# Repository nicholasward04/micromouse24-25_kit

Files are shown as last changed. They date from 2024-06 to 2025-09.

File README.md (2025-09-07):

The following repository will contain the work I've done as lead of the UCI Micromouse program. Some of the files included are inaccessible shortcuts and are generally administrative in nature. If you would like access please contact me at 818-233-1594 or nnward2004@icloud.com. 

The PCB is iterative and has had 2 other collaborators work on it in previous years. The PCB design was done in KiCAD 7.0 and the STM32 will be programmed using the STM32CubeIDE. I've changed the motor driver to something more capable than the L293D, added a circuit to protect the microcontroller when both the battery and STLINK are being used in full, and added an extra button. The PCB is 4-layer board with 3 GND planes and 1 power plane (split into +5V and +3V3 sections). I rerouted the entire board to fit in the new circuitry while maintaining the legacy aspects of the schematic. 
There are 2 versions of the design, one using an STM32 bluepill and one using solely the STM32F103C8T6 chip. This is to provide the option for teams that are part of the program to route their own boards using either one. 

Below is the relevant schematic.


Version using STM32 Bluepill front and back. The middle 2 layers of the board are mostly empty asides from a few traces and a GND and power plane, and therefore will not be included by image.

  

Version using STM32F103C8T6 chip front and back. Same as previous in terms of middle 2 layers. 

  

The software is split into 3 main components:
  1. The simulation
  2. The debugging GUI
  3. The firmware
<br>
1. The first part I worked on was my maze-solving algorithm in mackorone's micromouse simulator (https://github.com/mackorone/mms). Below is a gif of such:
Example
<br>
2. In parallel with the firmware, I developed a debugging tool using the Python Tkinter library, communicating with a UART bluetooth module on board my micromouse. This tool wasn't fully completed, but was useful for viewing telemetry from my mouse, such as IR sensor readings and battery voltage. If I were to do it again, I would have developed it in Visual Studio using C#, since the toolkits are much more advanced and easier to work with. Nevertheless, it was a good experience implementing wireless communication across a UART serial interface. Below is an image of the tool:
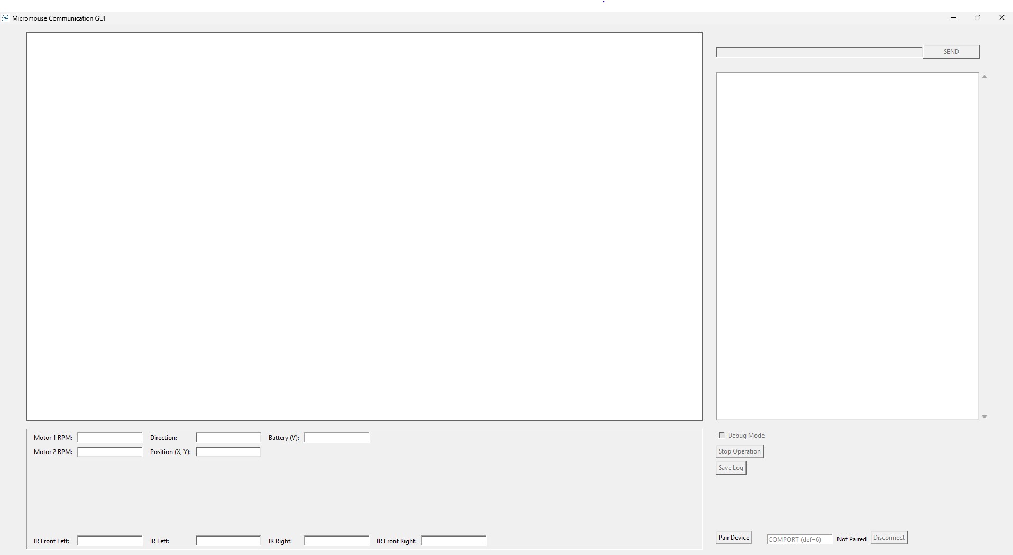
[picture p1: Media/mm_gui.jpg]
Example

<br>
3. Lastly, and most importantly, the firmware for my mouse was devleoped in C using the STM32CubeIDE. Below is a link to my best run at competition, where I placed 4th overall:
  
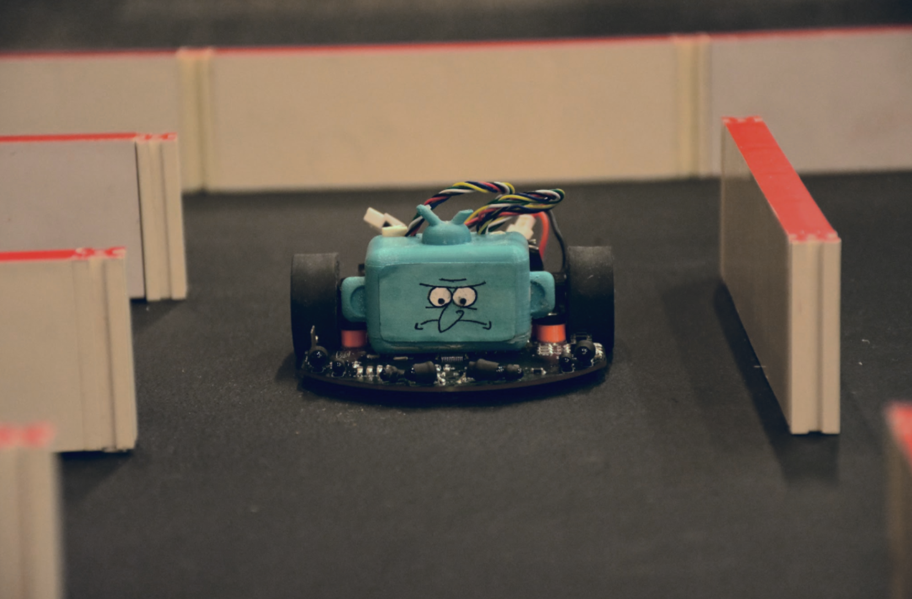
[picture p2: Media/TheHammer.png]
(https://www.youtube.com/live/5uL4w6jP68s?si=986Pjw4Ats6Im9Sl&t=11015)


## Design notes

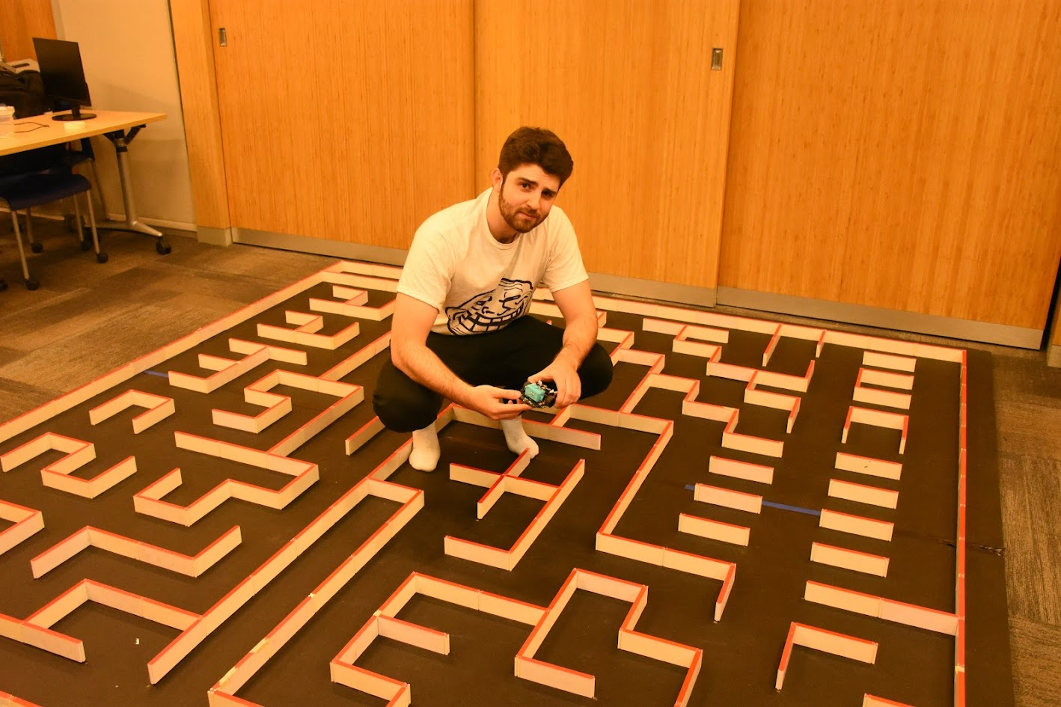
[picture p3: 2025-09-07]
Media/AAMC_2025.png

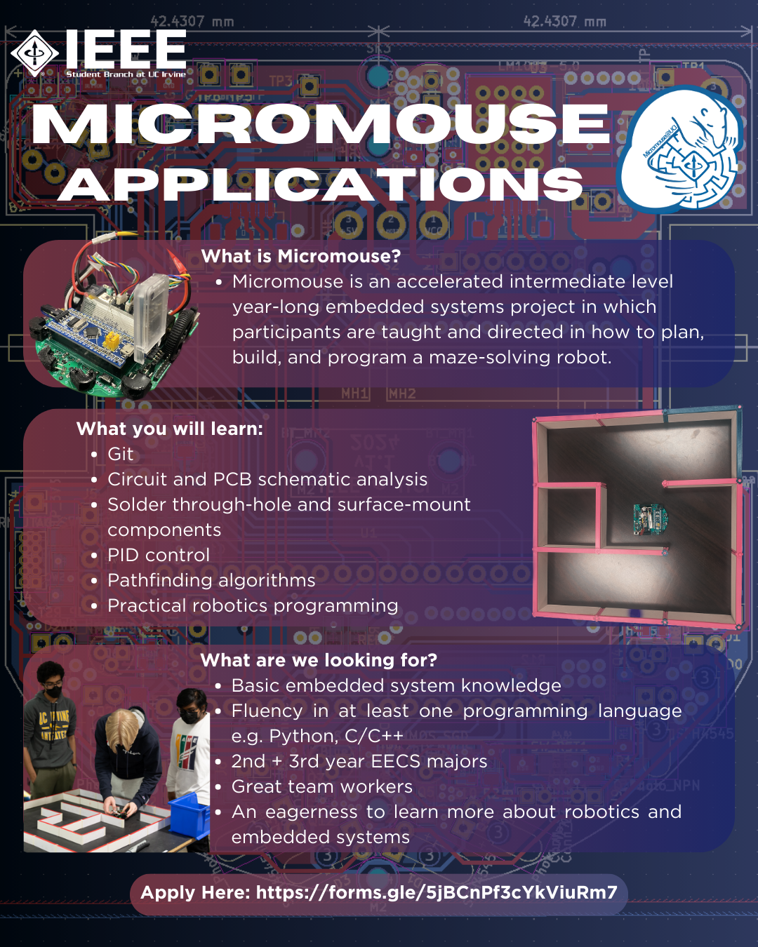
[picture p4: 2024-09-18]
Promotional/mm_flier_24-25no_qr.png

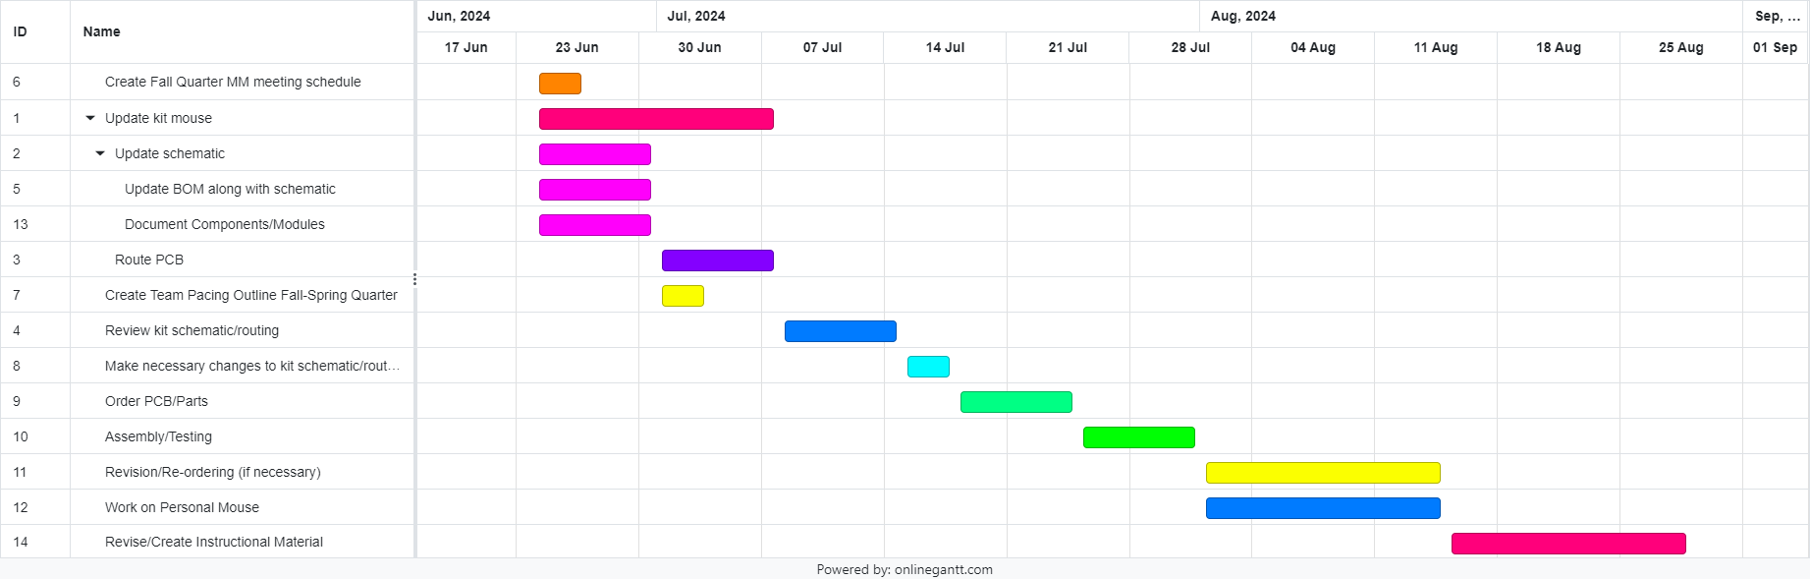
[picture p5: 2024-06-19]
Scheduling/MM24-25GanttChart_NW.png

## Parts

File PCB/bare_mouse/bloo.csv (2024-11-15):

Id | Designator | Footprint | Quantity | Designation | Supplier and ref
1 | D5,D4,D6 | LED_0805_2012Metric_Pad1.15x1.40mm_HandSolder | 3 | LED
2 | BZ1 | MagneticBuzzer_PUI_AT-0927-TT-6-R | 1 | Buzzer
3 | Q1,Q0,Q3,Q2 | Emitter | 4 | Q_Photo_NPN
4 | SW_RST1,SW2,SW1,SW3 | SW_SPST_REED_CT05-XXXX-G1 | 4 | SW
5 | D1,D3,D2,D0 | Emitter | 4 | SFH4545
6 | TP5,TP6,TP2 | PinHeader_1x01_P2.54mm_Vertical | 3 | GND_TP
7 | Q10,Q11,Q12,Q9 | SOT-23 | 4 | Q_NMOS_GSD
8 | BT1 | PinSocket_1x02_P2.54mm_Vertical | 1 | Battery_Cell
9 | J1 | PinHeader_1x06_P2.54mm_Vertical | 1 | Serial Debug Header
10 | R6,R8,R5,R7 | R_1206_3216Metric_Pad1.30x1.75mm_HandSolder | 4 | 35
11 | MOS1 | SOT-23F_TOS | 1 | SSM3K335R_LF
12 | J5,J2 | PinHeader_1x05_P2.54mm_Vertical | 2 | SWD Header
13 | C3,C21,C18,C15,C14,C17,C20 | C_1206_3216Metric_Pad1.33x1.80mm_HandSolder | 7 | 1uF
14 | C13,C4,C12,C1,C19 | C_1206_3216Metric_Pad1.33x1.80mm_HandSolder | 5 | 0.1uF
15 | R3,R1,R4,R2 | R_1206_3216Metric_Pad1.30x1.75mm_HandSolder | 4 | 1.8k
16 | U1 | STM32F103 | 1 | YAAJ_BluePill_SWD_Breakout
17 | TP1 | PinHeader_1x01_P2.54mm_Vertical | 1 | V_EXT_TP
18 | C10 | C_1206_3216Metric_Pad1.33x1.80mm_HandSolder | 1 | 10uF(Tantalum)
19 | U2 | DIP-16_W7.62mm | 1 | L293D
20 | SK2,SK1,SK4,SK3 | MountingHole_2.2mm_M2 | 4 | M2
21 | R19 | R_1206_3216Metric_Pad1.30x1.75mm_HandSolder | 1 | 750
22 | M_MH1,M_MH2 | Motor_mouse | 2 | M2
23 | R21,R20 | R_1206_3216Metric_Pad1.30x1.75mm_HandSolder | 2 | 75
24 | TP4 | PinHeader_1x01_P2.54mm_Vertical | 1 | TP_3V3
25 | TP3 | PinHeader_1x01_P2.54mm_Vertical | 1 | TP_5V
26 | M2 | Motor Headers | 1 | M2_Conn_Alt
27 | U6,U5 | DCK6_TEX | 2 | LM66100DCKR
28 | C11,C9 | C_1206_3216Metric_Pad1.33x1.80mm_HandSolder | 2 | 10uF
29 | U3 | 5V Voltage Reg | 1 | LM1085-5.0
30 | L1 | L_1206_3216Metric_Pad1.42x1.75mm_HandSolder | 1 | 10uH
31 | J4 | PinHeader_2x05_P1.27mm_Vertical | 1 | Conn_ARM_JTAG_SWD_10
32 | C2,C16 | CP_Radial_D6.3mm_P2.50mm | 2 | 100uF
33 | S1 | MM Switch | 1 | EG1218
34 | M1 | Motor Headers | 1 | M1_Conn_Alt
35 | R14,R13,R16,R17,R15 | R_1206_3216Metric_Pad1.30x1.75mm_HandSolder | 5 | 47k
36 | JP4 | SolderJumper-2_P1.3mm_Bridged_Pad1.0x1.5mm | 1 | Jumper_2_Open
37 | J10 | PinSocket_1x06_P2.54mm_Vertical | 1 | Conn_01x06_Female
38 | R22 | R_1206_3216Metric_Pad1.30x1.75mm_HandSolder | 1 | 20K
39 | FB4,FB3 | R_0603_1608Metric_Pad0.98x0.95mm_HandSolder | 2 | HZ0603C601R-10
40 | C25 | C_1206_3216Metric_Pad1.33x1.80mm_HandSolder | 1 | 10nF
41 | R23 | R_1206_3216Metric_Pad1.30x1.75mm_HandSolder | 1 | 10K
42 | JP2 | SolderJumper-2_P1.3mm_Open_Pad1.0x1.5mm | 1 | JP_GND
43 | JP1 | SolderJumper-2_P1.3mm_Open_Pad1.0x1.5mm | 1 | JP_SWO
44 | Q8 | SOT-23 | 1 | Q_NMOS_SGD
45 | C6,C8 | C_0603_1608Metric_Pad1.08x0.95mm_HandSolder | 2 | 22pF
46 | R18 | R_1206_3216Metric_Pad1.30x1.75mm_HandSolder | 1 | 0
47 | U4 | SOT-23-5 | 1 | APE8865Y5-33-HF-3
48 | R24,R12,R9,R11 | R_1206_3216Metric_Pad1.30x1.75mm_HandSolder | 4 | 47K
49 | JP3 | SolderJumper-2_P1.3mm_Open_Pad1.0x1.5mm | 1 | JP_RST

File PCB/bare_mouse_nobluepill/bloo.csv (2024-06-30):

Source: | C:\Users\darth\OneDrive\Desktop\Micromouse 24-25\24-25\PCB\bare_mouse\bloo.kicad_sch
Date: | 6/29/2024 11:02:38 PM
Tool: | Eeschema 7.0.8
Generator: | C:\Program Files\KiCad\7.0\bin\scripting\plugins/bom_csv_grouped_by_value.py
Component Count: | 101
Collated Components:
Item | Qty | Reference(s) | Value | LibPart | Footprint | Datasheet | DNP | Category | DK_Datasheet_Link | DK_Detail_Page | Description | Digi-Key_PN | Family | MPN | Manufacturer | Status
1 | 1 | BT1 | Battery_Cell | bloo-rescue:Battery_Cell-Device-mouse_v2-rescue | Connector_PinSocket_2.54mm:PinSocket_1x02_P2.54mm_Vertical
2 | 8 | BT_MH1, BT_MH2, BT_MH3, BT_MH4, SK1, SK2, SK3, SK4 | M2 | bloo-rescue:MountingHole-Mechanical-mouse_v2-rescue | MountingHole:MountingHole_2.2mm_M2
3 | 1 | BZ1 | Buzzer | bloo-rescue:Buzzer-Device-mouse_v2-rescue | custom_foot:buzzer
4 | 6 | C1, C4, C5, C12, C13, C19 | 0.1uF | Device:C | Capacitor_SMD:C_1206_3216Metric_Pad1.33x1.80mm_HandSolder | ~
5 | 2 | C2, C16 | 100uF | Device:C | Capacitor_THT:CP_Radial_D6.3mm_P2.50mm | ~
6 | 3 | C3, C7, C11 | 10uF | Device:C | Capacitor_SMD:C_1206_3216Metric_Pad1.33x1.80mm_HandSolder | ~
7 | 2 | C6, C8 | 22pF | Device:C_Small | Capacitor_SMD:C_0603_1608Metric_Pad1.08x0.95mm_HandSolder | ~
8 | 1 | C9 | 10uF | bloo-rescue:CP1-Device-mouse_v2-rescue | Capacitor_SMD:C_1206_3216Metric_Pad1.33x1.80mm_HandSolder
9 | 1 | C10 | 10uF(Tantalum) | bloo-rescue:CP1-Device-mouse_v2-rescue | Capacitor_SMD:C_1206_3216Metric_Pad1.33x1.80mm_HandSolder
10 | 6 | C14, C15, C17, C18, C20, C21 | 1uF | Device:C | Capacitor_SMD:C_1206_3216Metric_Pad1.33x1.80mm_HandSolder | ~
11 | 1 | C25 | 10nF | Device:C | Capacitor_SMD:C_1206_3216Metric_Pad1.33x1.80mm_HandSolder | ~
12 | 4 | D0, D1, D2, D3 | SFH4545 | bloo-rescue:IRL81A-LED-mouse_v2-rescue | MM_Library:Emitter | http://www.osram-os.com/Graphics/XPic0/00203825_0.pdf
13 | 3 | D4, D5, D6 | LED | bloo-rescue:LED-Device-mouse_v2-rescue | LED_SMD:LED_0805_2012Metric_Pad1.15x1.40mm_HandSolder
14 | 2 | FB3, FB4 | HZ0603C601R-10 | Device:FerriteBead_Small | Resistor_SMD:R_0603_1608Metric_Pad0.98x0.95mm_HandSolder | ~
15 | 1 | J1 | Serial Debug Header | Connector:Conn_01x06_Female | Connector_PinHeader_2.54mm:PinHeader_1x06_P2.54mm_Vertical | ~
16 | 1 | J4 | Conn_ARM_JTAG_SWD_10 | Connector:Conn_ARM_JTAG_SWD_10 | Connector_PinHeader_1.27mm:PinHeader_2x05_P1.27mm_Vertical | http://infocenter.arm.com/help/topic/com.arm.doc.ddi0314h/DDI0314H_coresight_components_trm.pdf
17 | 1 | J5 | SWD Header | Connector:Conn_01x05_Male | Connector_PinHeader_2.54mm:PinHeader_1x05_P2.54mm_Vertical | ~
18 | 1 | J10 | Conn_01x06_Female | Connector:Conn_01x06_Female | Connector_PinSocket_2.54mm:PinSocket_1x06_P2.54mm_Vertical | ~
19 | 1 | JP1 | JP_SWO | Jumper:SolderJumper_2_Open | Jumper:SolderJumper-2_P1.3mm_Open_Pad1.0x1.5mm | ~
20 | 1 | JP2 | JP_GND | Jumper:SolderJumper_2_Open | Jumper:SolderJumper-2_P1.3mm_Open_Pad1.0x1.5mm | ~
21 | 1 | JP3 | JP_RST | Jumper:SolderJumper_2_Open | Jumper:SolderJumper-2_P1.3mm_Open_Pad1.0x1.5mm | ~
22 | 1 | JP4 | Jumper_2_Open | Jumper:Jumper_2_Open | Jumper:SolderJumper-2_P1.3mm_Bridged_Pad1.0x1.5mm | ~
23 | 1 | L1 | 10uH | Device:L | Inductor_SMD:L_1206_3216Metric_Pad1.42x1.75mm_HandSolder | ~
24 | 1 | M1 | M1_Conn_Alt | Connector:Conn_01x06_Female | MM_Library:Motor Headers | ~
25 | 1 | M2 | M2_Conn_Alt | Connector:Conn_01x06_Female | MM_Library:Motor Headers | ~
26 | 2 | M_MH1, M_MH2 | M2 | bloo-rescue:MountingHole-Mechanical-mouse_v2-rescue | MM_Library:Motor_mouse
27 | 4 | Q0, Q1, Q2, Q3 | TEFT4300 | bloo-rescue:Q_Photo_NPN-Device-mouse_v2-rescue | MM_Library:Emitter
28 | 1 | Q8 | Q_NMOS_SGD | Device:Q_NMOS_SGD | Package_TO_SOT_SMD:SOT-23 | ~
29 | 4 | Q9, Q10, Q11, Q12 | Q_NMOS_GSD | Device:Q_NMOS_GSD | Package_TO_SOT_SMD:SOT-23 | ~
30 | 4 | R1, R2, R3, R4 | 1.8k | bloo-rescue:R-Device-mouse_v2-rescue | Resistor_SMD:R_1206_3216Metric_Pad1.30x1.75mm_HandSolder
31 | 4 | R5, R6, R7, R8 | 35 | bloo-rescue:R-Device-mouse_v2-rescue | Resistor_SMD:R_1206_3216Metric_Pad1.30x1.75mm_HandSolder
32 | 2 | R9, R10 | 100K | Device:R | Resistor_SMD:R_1206_3216Metric_Pad1.30x1.75mm_HandSolder | ~
33 | 3 | R11, R12, R24 | 47K | Device:R | Resistor_SMD:R_1206_3216Metric_Pad1.30x1.75mm_HandSolder | ~
34 | 5 | R13, R14, R15, R16, R17 | 47k | bloo-rescue:R-Device-mouse_v2-rescue | Resistor_SMD:R_1206_3216Metric_Pad1.30x1.75mm_HandSolder
35 | 1 | R18 | R | Device:R | Resistor_SMD:R_1206_3216Metric_Pad1.30x1.75mm_HandSolder | ~
36 | 1 | R19 | 750 | bloo-rescue:R-Device-mouse_v2-rescue | Resistor_SMD:R_1206_3216Metric_Pad1.30x1.75mm_HandSolder
37 | 2 | R20, R21 | 75 | bloo-rescue:R-Device-mouse_v2-rescue | Resistor_SMD:R_1206_3216Metric_Pad1.30x1.75mm_HandSolder
38 | 1 | R22 | 20K | Device:R | Resistor_SMD:R_1206_3216Metric_Pad1.30x1.75mm_HandSolder | ~
39 | 1 | R23 | 10K | Device:R | Resistor_SMD:R_1206_3216Metric_Pad1.30x1.75mm_HandSolder | ~
40 | 1 | S1 | EG1218 | bloo-rescue:EG1218-dk_Slide-Switches-mouse-rescue | MM_Library:MM Switch | http://spec_sheets.e-switch.com/specs/P040040.pdf |  | Switches | http://spec_sheets.e-switch.com/specs/P040040.pdf | /product-detail/en/e-switch/EG1218/EG1903-ND/101726 | SWITCH SLIDE SPDT 200MA 30V | EG1903-ND | Slide Switches | EG1218 | E-Switch | Active
41 | 3 | SW1, SW2, SW_RST1 | SW | Switch:SW_Push | Button_Switch_SMD:SW_SPST_REED_CT05-XXXX-G1 | ~
42 | 1 | TP1 | V_EXT_TP | Connector:TestPoint | Connector_PinHeader_2.54mm:PinHeader_1x01_P2.54mm_Vertical | ~
43 | 3 | TP2, TP5, TP6 | GND_TP | Connector:TestPoint | Connector_PinHeader_2.54mm:PinHeader_1x01_P2.54mm_Vertical | ~
44 | 1 | TP3 | TP_5V | Connector:TestPoint | Connector_PinHeader_2.54mm:PinHeader_1x01_P2.54mm_Vertical | ~
45 | 1 | TP4 | TP_3V3 | Connector:TestPoint | Connector_PinHeader_2.54mm:PinHeader_1x01_P2.54mm_Vertical | ~
46 | 1 | U1 | YAAJ_BluePill_SWD_Breakout | YAAJ_BluePill_SWD_Breakout:YAAJ_BluePill_SWD_Breakout | MM_Library:STM32F103
47 | 1 | U2 | TB6612FNG | Driver_Motor:TB6612FNG | Package_SO:SSOP-24_5.3x8.2mm_P0.65mm | https://toshiba.semicon-storage.com/us/product/linear/motordriver/detail.TB6612FNG.html
48 | 1 | U3 | LM1085-5.0 | bloo-rescue:LM1084-5.0-Regulator_Linear-mouse_v2-rescue | MM_Library:5V Voltage Reg | http://www.ti.com/lit/ds/symlink/lm1084.pdf
49 | 1 | U4 | APE8865Y5-33-HF-3 | Regulator_Linear:APE8865Y5-33-HF-3 | Package_TO_SOT_SMD:SOT-23-5 | http://www.tme.eu/fr/Document/ced3461ed31ea70a3c416fb648e0cde7/APE8865-3.pdf

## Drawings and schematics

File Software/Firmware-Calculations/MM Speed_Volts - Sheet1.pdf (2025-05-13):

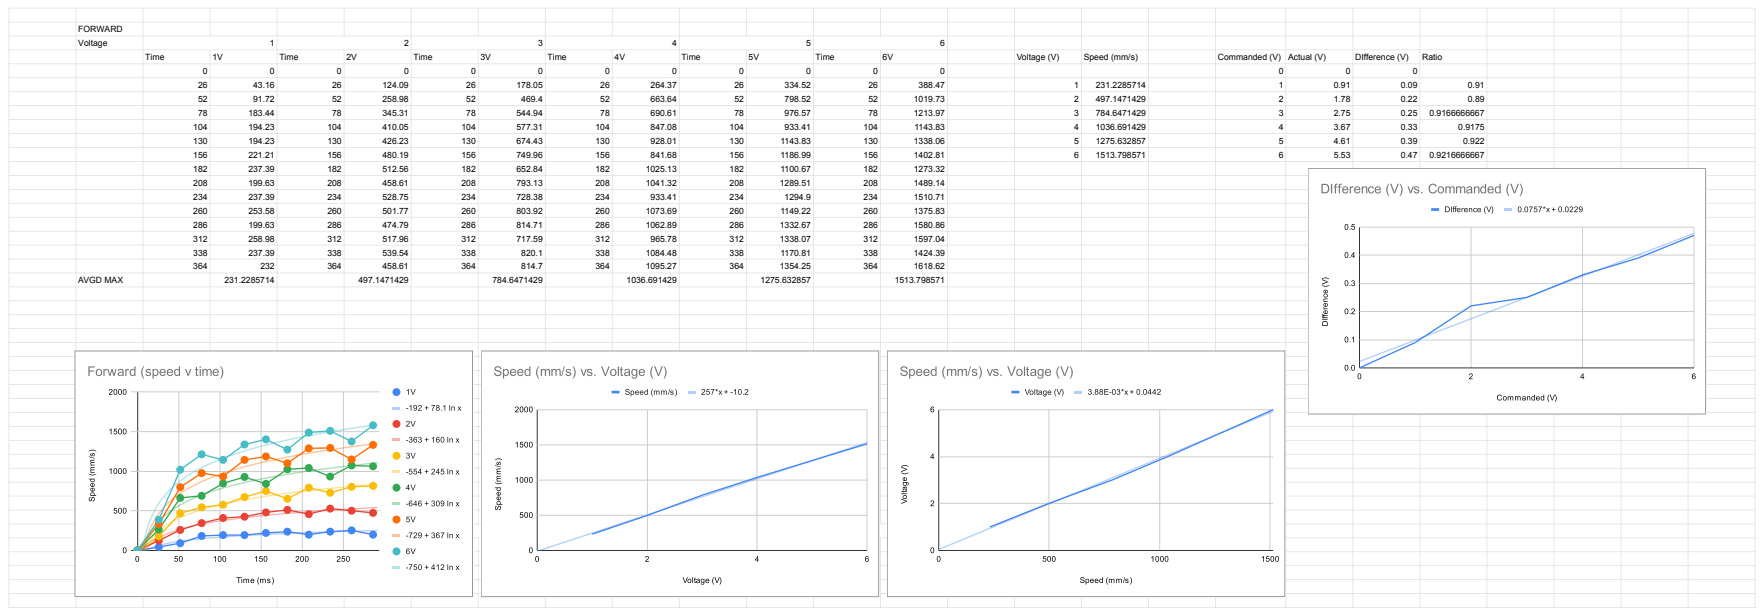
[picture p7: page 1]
FORWARD; Voltage; 6 Time; Time; Voltage (V); Speed (mm/s); Commanded (V) Actual (V); DIfference (V); Ratio; 1618.62 AVGD MAX

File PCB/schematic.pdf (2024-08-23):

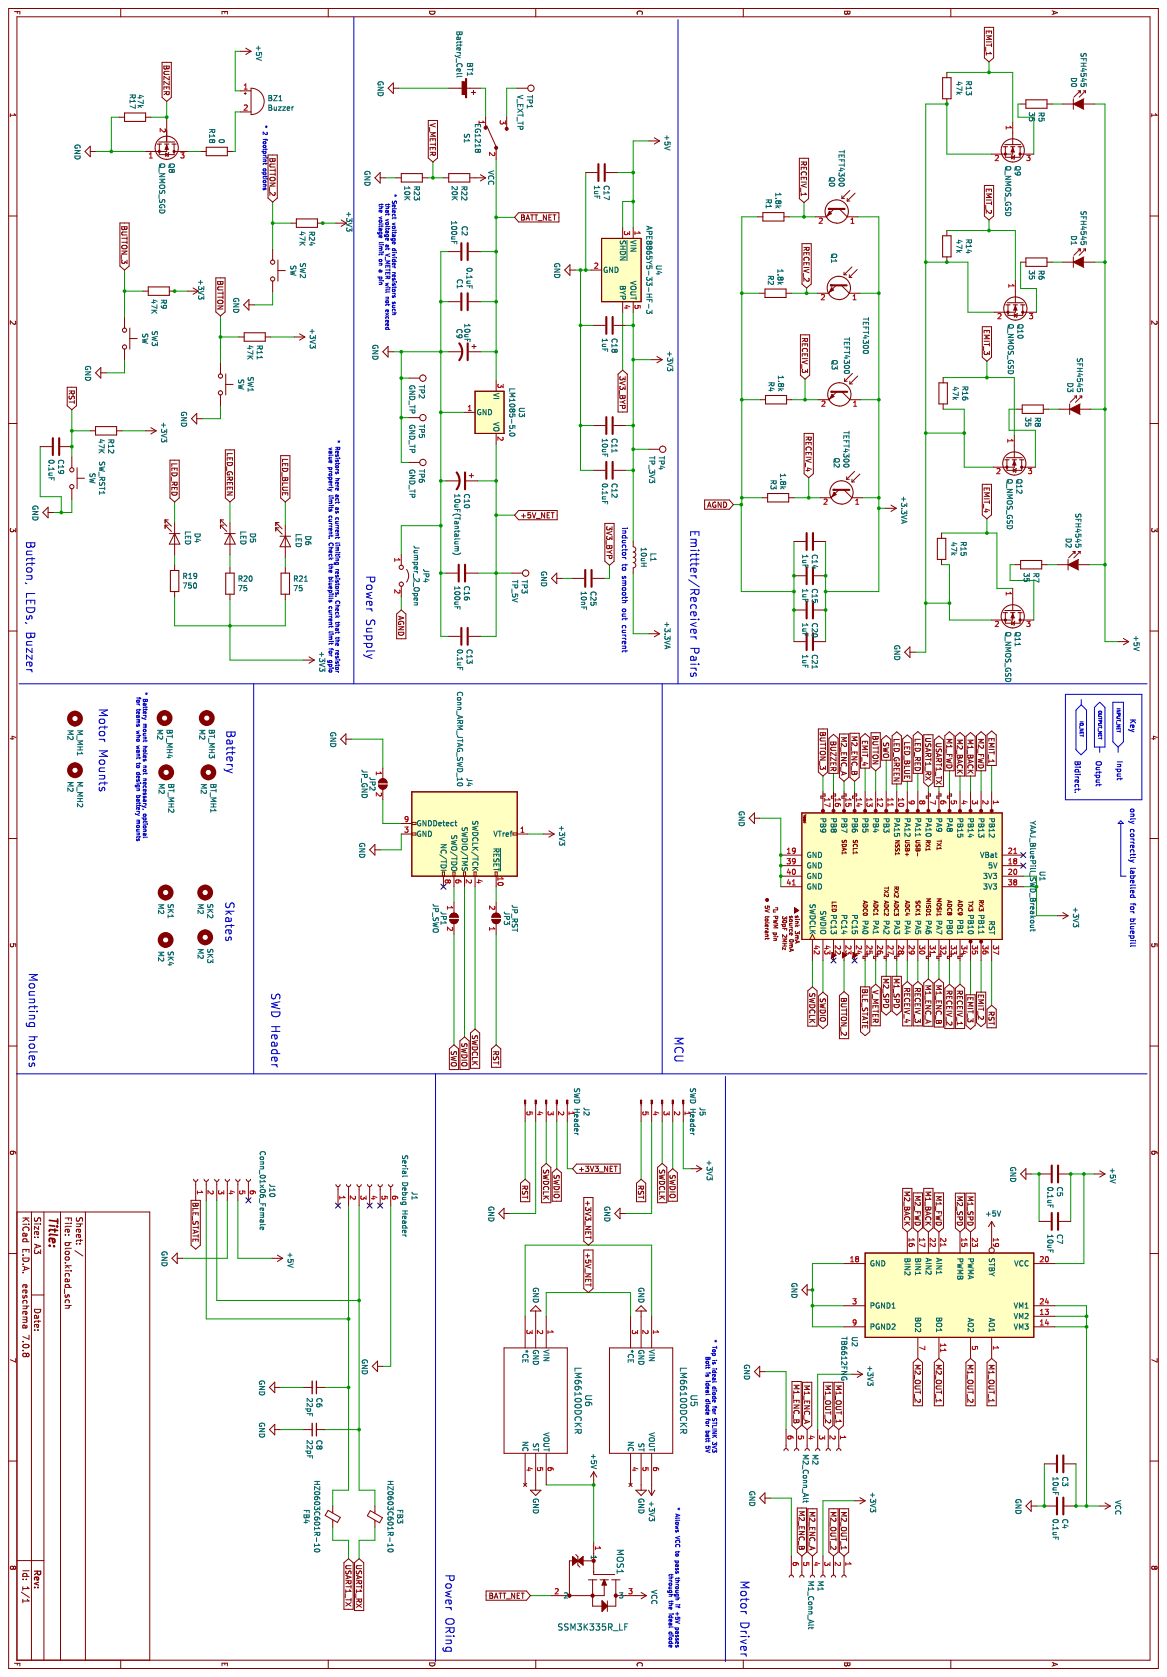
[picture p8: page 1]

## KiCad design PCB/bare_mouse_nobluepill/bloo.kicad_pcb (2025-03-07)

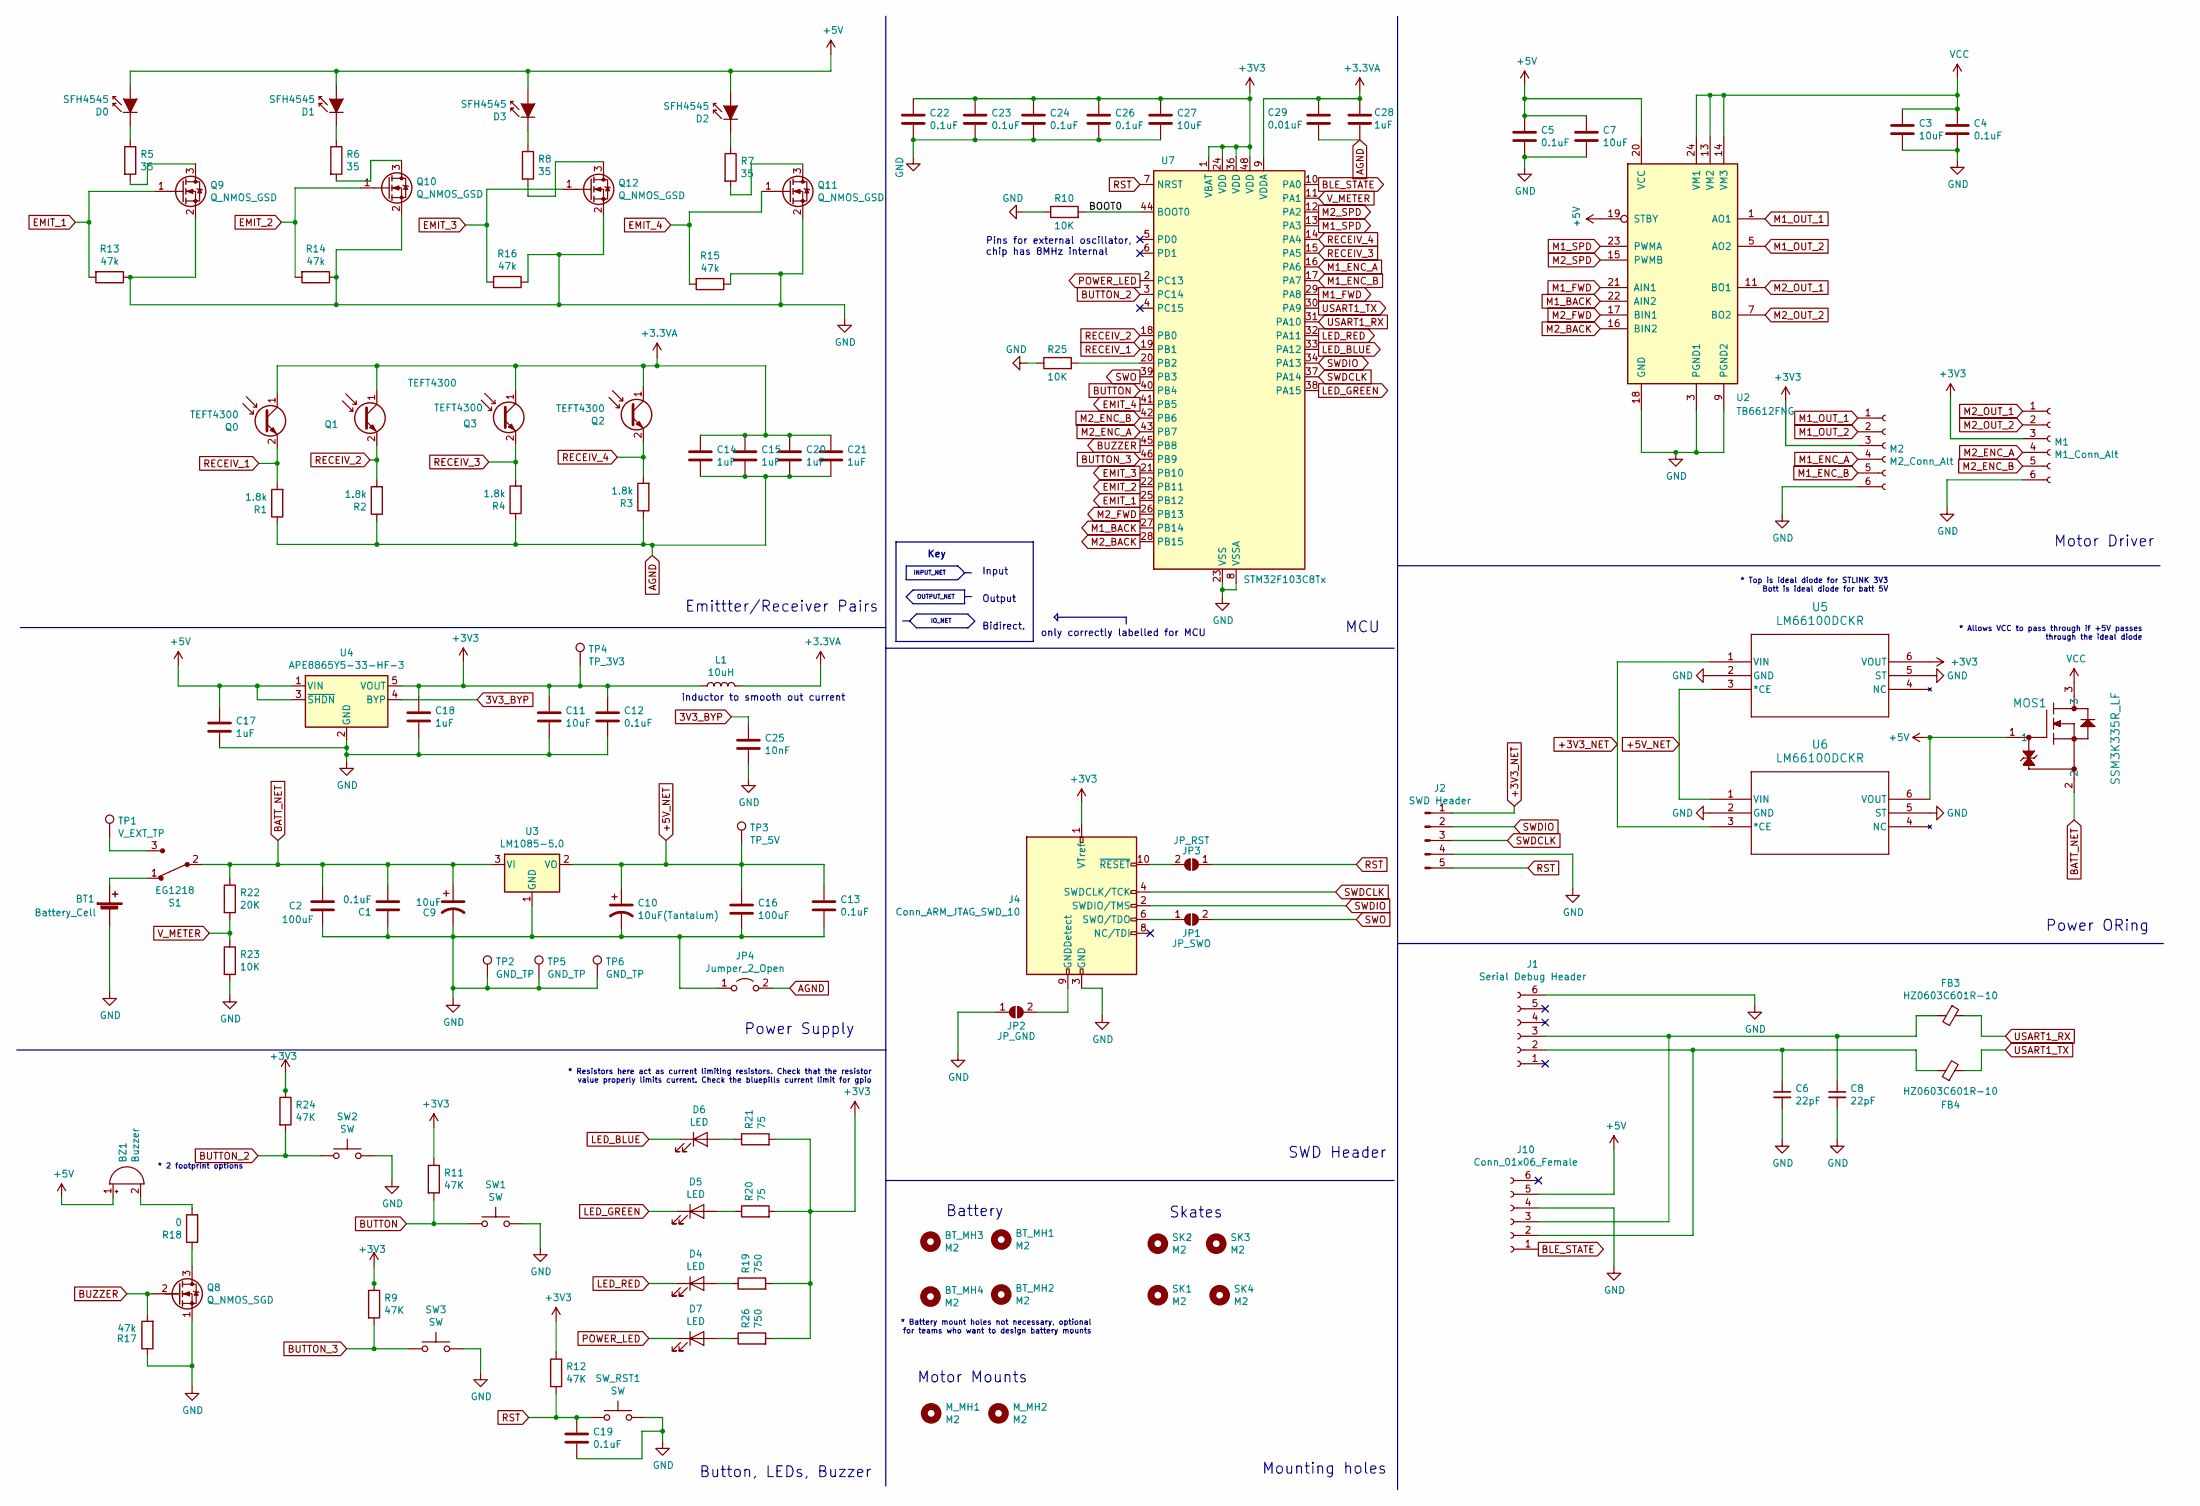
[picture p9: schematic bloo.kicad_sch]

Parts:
BT1: Battery_Cell; PinSocket_1x02_P2.54mm_Vertical
BT_MH1, BT_MH2, BT_MH3, BT_MH4: M2; MountingHole_2.2mm_M2
BZ1: Buzzer; MagneticBuzzer_PUI_AT-0927-TT-6-R
C1, C4, C5, C12, C13, C19, C22, C23, C24, C26: 0.1uF; C_1206_3216Metric_Pad1.33x1.80mm_HandSolder
C2, C16: 100uF; CP_Radial_D6.3mm_P2.50mm
C3, C7, C9, C11, C27: 10uF; C_1206_3216Metric_Pad1.33x1.80mm_HandSolder
C6, C8: 22pF; C_0603_1608Metric_Pad1.08x0.95mm_HandSolder
C10: 10uF(Tantalum); C_1206_3216Metric_Pad1.33x1.80mm_HandSolder
C14, C15, C17, C18, C20, C21, C28: 1uF; C_1206_3216Metric_Pad1.33x1.80mm_HandSolder
C25: 10nF; C_1206_3216Metric_Pad1.33x1.80mm_HandSolder
C29: 0.01uF; C_1206_3216Metric_Pad1.33x1.80mm_HandSolder
D0, D1, D2, D3: SFH4545; Emitter
D4, D5, D6, D7: LED; LED_0805_2012Metric_Pad1.15x1.40mm_HandSolder
FB3, FB4: HZ0603C601R-10; R_0603_1608Metric_Pad0.98x0.95mm_HandSolder
J1: Serial Debug Header; PinHeader_1x06_P2.54mm_Vertical
J2: SWD Header; PinHeader_1x05_P2.54mm_Vertical
J4: Conn_ARM_JTAG_SWD_10; PinHeader_2x05_P1.27mm_Vertical
J10: Conn_01x06_Female; PinSocket_1x06_P2.54mm_Vertical
JP1: JP_SWO; SolderJumper-2_P1.3mm_Open_Pad1.0x1.5mm
JP2: JP_GND; SolderJumper-2_P1.3mm_Open_Pad1.0x1.5mm
JP3: JP_RST; SolderJumper-2_P1.3mm_Open_Pad1.0x1.5mm
JP4: Jumper_2_Open; SolderJumper-2_P1.3mm_Bridged_Pad1.0x1.5mm
L1: 10uH; L_1206_3216Metric_Pad1.42x1.75mm_HandSolder
M1: M1_Conn_Alt; Motor Headers
M2: M2_Conn_Alt; Motor Headers
MOS1: SSM3K335R_LF; SOT-23F_TOS
M_MH1, M_MH2: M2; Motor_mouse
Q0, Q1, Q2, Q3: TEFT4300; Emitter
Q8: Q_NMOS_SGD; SOT-23
Q9, Q10, Q11, Q12: Q_NMOS_GSD; SOT-23
R1, R2, R3, R4: 1.8k; R_1206_3216Metric_Pad1.30x1.75mm_HandSolder
R5, R6, R7, R8: 35; R_1206_3216Metric_Pad1.30x1.75mm_HandSolder
R9, R11, R12, R24: 47K; R_1206_3216Metric_Pad1.30x1.75mm_HandSolder
R10, R23, R25: 10K; R_1206_3216Metric_Pad1.30x1.75mm_HandSolder
R13, R14, R15, R16, R17: 47k; R_1206_3216Metric_Pad1.30x1.75mm_HandSolder
R18: 0; R_1206_3216Metric_Pad1.30x1.75mm_HandSolder
R19, R26: 750; R_1206_3216Metric_Pad1.30x1.75mm_HandSolder
R20, R21: 75; R_1206_3216Metric_Pad1.30x1.75mm_HandSolder
R22: 20K; R_1206_3216Metric_Pad1.30x1.75mm_HandSolder
S1: EG1218; MM Switch; MPN EG1218; Digi-Key_PN EG1903-ND
SK1, SK2, SK3, SK4: M2; MountingHole_2.2mm_M2
SW1, SW2, SW3: SW; SW_SPST_REED_CT05-XXXX-G1
SW_RST1: SW; SW_SPST_REED_CT05-XXXX-G1
TP1: V_EXT_TP; PinHeader_1x01_P2.54mm_Vertical
TP2, TP5, TP6: GND_TP; PinHeader_1x01_P2.54mm_Vertical
TP3: TP_5V; PinHeader_1x01_P2.54mm_Vertical
TP4: TP_3V3; PinHeader_1x01_P2.54mm_Vertical
U2: TB6612FNG; SSOP-24_5.3x8.2mm_P0.65mm
U3: LM1085-5.0; 5V Voltage Reg
U4: APE8865Y5-33-HF-3; SOT-23-5
U5, U6: LM66100DCKR; DCK6_TEX
U7: STM32F103C8Tx; LQFP-48_7x7mm_P0.5mm

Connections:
3V3_BYP: C25.1, U4.4 (BYP)
+3.3VA: C14.1, C15.1, C20.1, C21.1, C28.1, C29.1, L1.2, Q0.1 (C), Q1.1 (C), Q2.1 (C), Q3.1 (C), U7.9 (VDDA)
+3V3: C11.1, C12.1, C18.1, C22.1, C23.1, C24.1, C26.1, C27.1, J4.1 (VTref), L1.1, M1.3, M2.3, R9.1, R11.1, R12.1, R19.2, R20.2, R21.2, R24.1, R26.2, TP4.1, U4.5 (VOUT), U5.6 (VOUT), U7.1 (VBAT), U7.24 (VDD), U7.36 (VDD), U7.48 (VDD)
+3V3_NET: J2.1, U5.1 (VIN), U6.3 (*CE)
+5V: BZ1.1 (-), C5.1, C7.1, C17.1, D0.2 (A), D1.2 (A), D2.2 (A), D3.2 (A), J10.5, MOS1.1, U2.19 (STBY), U2.20 (VCC), U4.1 (VIN), U4.3 (~SHDN), U6.6 (VOUT)
+5V_NET: C10.1, C13.1, C16.1, TP3.1, U3.2 (VO), U5.3 (*CE), U6.1 (VIN)
/BOOT0: R10.2, U7.44 (BOOT0)
AGND: C14.2, C15.2, C20.2, C21.2, C28.2, C29.2, JP4.2 (B), R1.1, R2.1, R3.1, R4.1
BLE_STATE: J10.1, U7.10 (PA0)
BUTTON: R11.2, SW1.1, U7.40 (PB4)
BUTTON_2: R24.2, SW2.1, U7.3 (PC14)
BUTTON_3: R9.2, SW3.1, U7.46 (PB9)
BUZZER: Q8.2 (G), R17.2, U7.45 (PB8)
EMIT_1: Q9.1 (G), R13.2, U7.25 (PB12)
EMIT_2: Q10.1 (G), R14.2, U7.22 (PB11)
EMIT_3: Q12.1 (G), R16.2, U7.21 (PB10)
EMIT_4: Q11.1 (G), R15.2, U7.41 (PB5)
GND: BT1.2 (-), C1.1, C2.2, C3.2, C4.2, C5.2, C6.2, C7.2, C8.2, C9.2, C10.2, C11.2, C12.2, C13.2, C16.2, C17.2, C18.2, C19.2, C22.2, C23.2, C24.2, C25.2, C26.2, C27.2, J1.6, J2.4, J4.3 (GND), J4.5 (GND), J10.4, JP2.1 (A), JP4.1 (A), M1.6, M2.6, Q8.1 (S), Q9.2 (S), Q10.2 (S), Q11.2 (S), Q12.2 (S), R10.1, R13.1, R14.1, R15.1, R16.1, R17.1, R23.2, R25.1, SW1.2, SW2.2, SW3.2, SW_RST1.2, TP2.1, TP5.1, TP6.1, U2.3 (PGND1), U2.4 (PGND1), U2.9 (PGND2), U2.10 (PGND2), U2.18 (GND), U3.1 (GND), U4.2 (GND), U5.2 (GND), U5.5 (ST), U6.2 (GND), U6.5 (ST), U7.8 (VSSA), U7.23 (VSS), U7.35 (VSS), U7.47 (VSS); also elsewhere on the board
LED_BLUE: D6.1 (K), U7.33 (PA12)
LED_GREEN: D5.1 (K), U7.38 (PA15)
LED_RED: D4.1 (K), U7.32 (PA11)
M1_BACK: U2.22 (AIN2), U7.27 (PB14)
M1_ENC_A: M2.4, U7.16 (PA6)
M1_ENC_B: M2.5, U7.17 (PA7)
M1_FWD: U2.21 (AIN1), U7.29 (PA8)
M1_OUT_1: M2.1, U2.1 (AO1), U2.2 (AO1)
M1_OUT_2: M2.2, U2.5 (AO2), U2.6 (AO2)
M1_SPD: U2.23 (PWMA), U7.13 (PA3)
M2_BACK: U2.16 (BIN2), U7.28 (PB15)
M2_ENC_A: M1.4, U7.43 (PB7)
M2_ENC_B: M1.5, U7.42 (PB6)
M2_FWD: U2.17 (BIN1), U7.26 (PB13)
M2_OUT_1: M1.1, U2.11 (BO1), U2.12 (BO1)
M2_OUT_2: M1.2, U2.7 (BO2), U2.8 (BO2)
M2_SPD: U2.15 (PWMB), U7.12 (PA2)
unnamed: BT1.1 (+), S1.1
unnamed: BZ1.2 (+), R18.2
unnamed: D0.1 (K), R5.1
unnamed: D1.1 (K), R6.1
unnamed: D2.1 (K), R7.1
unnamed: D3.1 (K), R8.1
unnamed: D4.2 (A), R19.1
unnamed: D5.2 (A), R20.1
unnamed: D6.2 (A), R21.1
unnamed 44: D7.2 (A), R26.1; also elsewhere on the board
unnamed: C6.1, FB4.1, J1.2, J10.2
unnamed: C8.1, FB3.2, J1.3, J10.3
unnamed: J4.9 (GNDDetect), JP2.2 (B)
unnamed: J4.6 (SWO/TDO), JP1.1 (A)
unnamed: J4.10 (~RESET), JP3.2 (B)
unnamed: Q8.3 (D), R18.1
unnamed: Q9.3 (D), R5.2
unnamed: Q10.3 (D), R6.2
unnamed: Q11.3 (D), R7.2
unnamed: Q12.3 (D), R8.2
unnamed: S1.3, TP1.1
unnamed: R25.2, U7.20 (PB2)
POWER_LED: D7.1 (K), U7.2 (PC13); also elsewhere on the board
RECEIV_1: Q0.2 (E), R1.2, U7.19 (PB1)
RECEIV_2: Q1.2 (E), R2.2, U7.18 (PB0)
RECEIV_3: Q3.2 (E), R4.2, U7.15 (PA5)
RECEIV_4: Q2.2 (E), R3.2, U7.14 (PA4)
RST: C19.1, J2.5, JP3.1 (A), R12.2, SW_RST1.1, U7.7 (NRST); also elsewhere on the board
SWDCLK: J2.3, J4.4 (SWDCLK/TCK), U7.37 (PA14)
SWDIO: J2.2, J4.2 (SWDIO/TMS), U7.34 (PA13)
SWO: JP1.2 (B), U7.39 (PB3)
USART1_RX: FB3.1, U7.31 (PA10)
USART1_TX: FB4.2, U7.30 (PA9)
V_METER: R22.2, R23.1, U7.11 (PA1)

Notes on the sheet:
INPUT_NET
Mounting holes
Power ORing
Battery
Input
inductor to smooth out current
* 2 footprint options
* Battery mount holes not necessary, optional for teams who want to design battery mounts
* Top is ideal diode for STLINK 3V3 Bott is ideal diode for batt 5V
Motor Driver
* Allows VCC to pass through if +5V passes through the ideal diode
Emittter/Receiver Pairs
* Resistors here act as current limiting resistors. Check that the resistor value properly limits current. Check the bluepills current limit for gpio
IO_NET
Output
MCU
Key
SWD Header
only correctly labelled for MCU
Motor Mounts
Button, LEDs, Buzzer
Skates
Power Supply
Bidirect.
OUTPUT_NET
Pins for external oscillator, chip has 8MHz internal

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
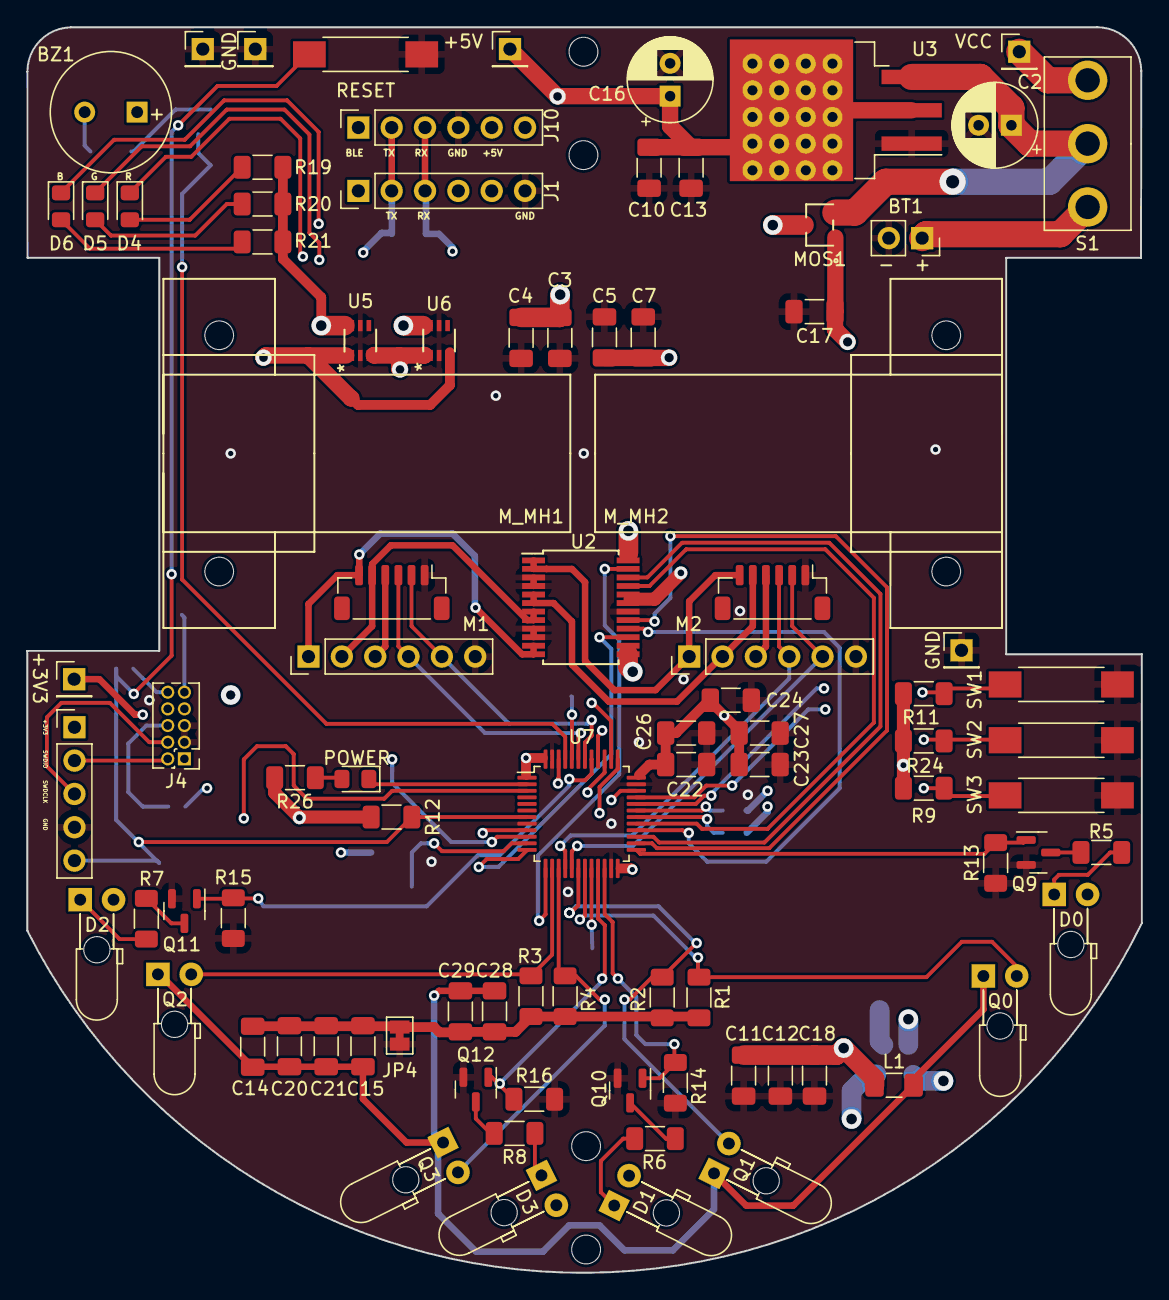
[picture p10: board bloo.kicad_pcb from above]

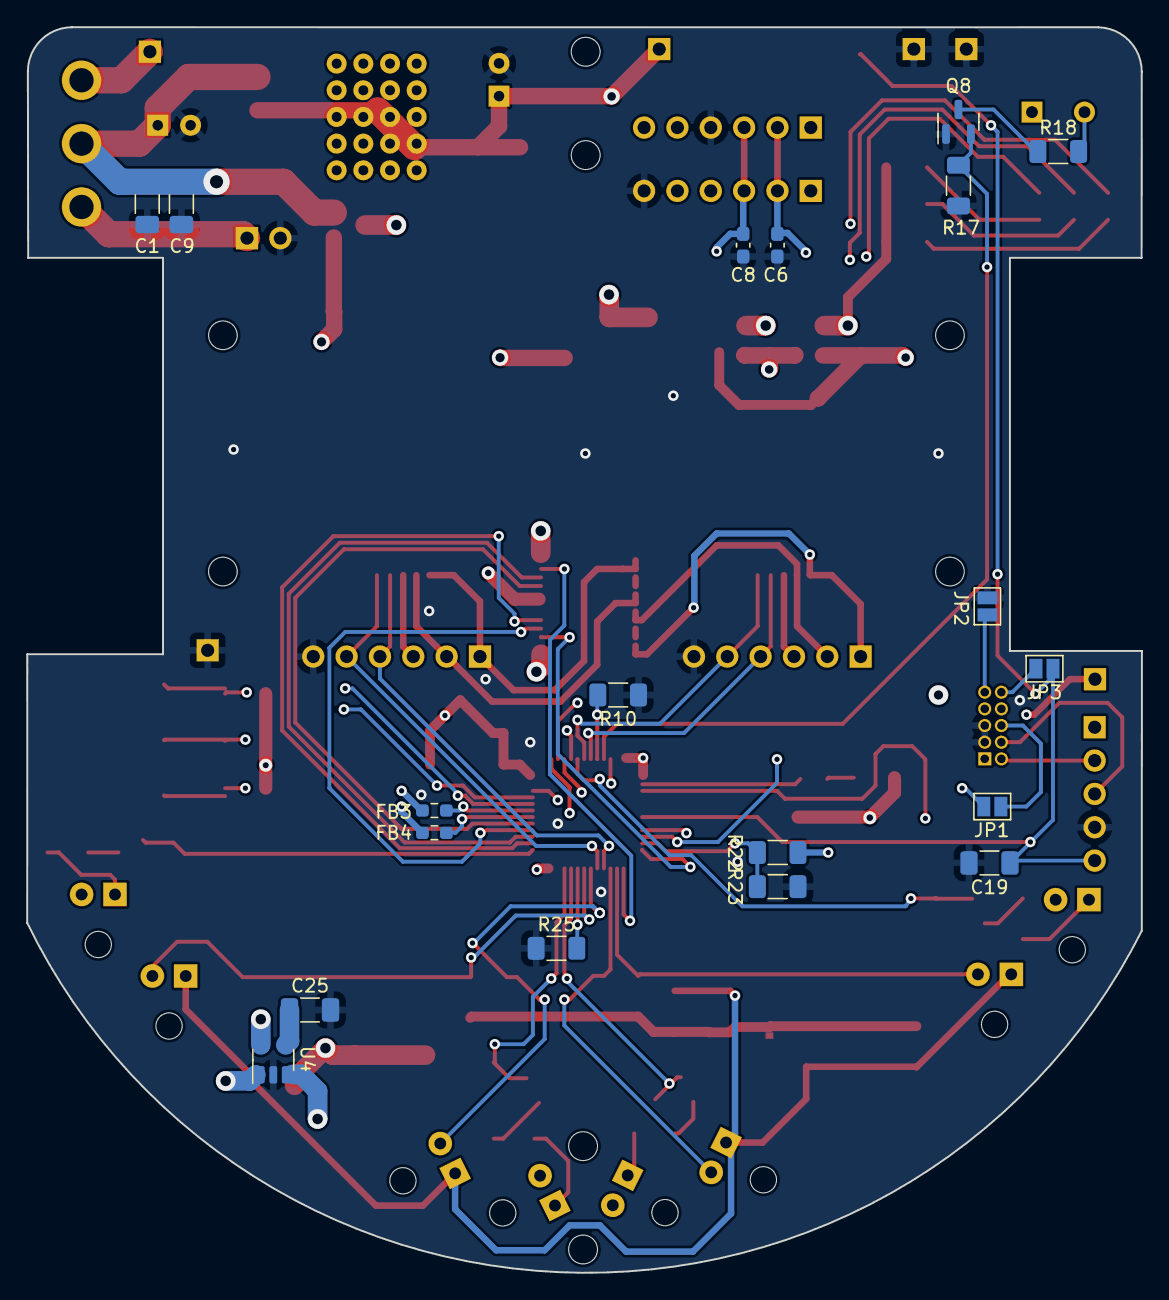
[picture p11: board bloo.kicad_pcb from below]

Board: 4 copper layers, 84.9 x 94.9 mm, 111 parts (19 on the bottom side), 71 nets.

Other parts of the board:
POWER: LED; LED_0805_2012Metric_Pad1.15x1.40mm_HandSolder
RESET: SW; SW_SPST_REED_CT05-XXXX-G1

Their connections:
GND: RESET.2; also elsewhere on the board
unnamed 44: POWER.2 (A); also elsewhere on the board
POWER_LED: POWER.1 (K); also elsewhere on the board
RST: RESET.1; also elsewhere on the board

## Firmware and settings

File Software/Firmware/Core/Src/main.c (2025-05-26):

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
/* Includes ------------------------------------------------------------------*/
#include "main.h"

/* USER CODE BEGIN Includes */
#include "mm_supplemental.h"
#include "mm_commands.h"
#include "mm_vision.h"
#include "mm_systick.h"
#include "mm_motors.h"
#include "mm_encoders.h"
#include "mm_floodfill.h"
#include "mm_profiles.h"
/* USER CODE END Includes */

ADC_HandleTypeDef hadc1;
ADC_HandleTypeDef hadc2;

TIM_HandleTypeDef htim2;
TIM_HandleTypeDef htim3;
TIM_HandleTypeDef htim4;

UART_HandleTypeDef huart1;

void SystemClock_Config(void);
static void MX_GPIO_Init(void);
static void MX_ADC1_Init(void);
static void MX_TIM2_Init(void);
static void MX_TIM3_Init(void);
static void MX_TIM4_Init(void);
static void MX_USART1_UART_Init(void);
static void MX_ADC2_Init(void);
/* USER CODE BEGIN 0 */
mouse_state_t mouse_state;

// Debug Mode
uint8_t debugMode = 0;
uint8_t debugCounter = 0;

// Global
uint32_t global_time = 0;
bool armed = false;

// IRs
extern bool adjust_steering;

// Encoders
int32_t objective_L = 0;
int32_t objective_R = 0;

// Maze-Solving
struct Maze maze;
uint8_t goal_swap = 0;

mouse_mode_t mouse_mode = SEARCHING;

// Profiles
profile_t forward_profile;
profile_t rotational_profile;

extern bool motor_controller_enabled;
extern param_t fwd_placeholder_1;
extern param_t fwd_placeholder_2;
extern param_t rot_placeholder_1;

/* USER CODE END 0 */

/**
  * @brief  The application entry point.
  * @retval int
  */
int main(void)
{

  /* MCU Configuration--------------------------------------------------------*/

  /* Reset of all peripherals, Initializes the Flash interface and the Systick. */
  HAL_Init();

  /* USER CODE BEGIN Init */
  LED_Power_Init();
  /* USER CODE END Init */

  /* Configure the system clock */
  SystemClock_Config();

  /* Initialize all configured peripherals */
  MX_GPIO_Init();
  MX_ADC1_Init();
  MX_TIM2_Init();
  MX_TIM3_Init();
  MX_TIM4_Init();
  MX_USART1_UART_Init();
  MX_ADC2_Init();
  /* USER CODE BEGIN 2 */
  uint8_t startBuff;
  HAL_UART_Receive_IT(&huart1, &startBuff, 1);

  HAL_TIM_PWM_Start(&htim2, TIM_CHANNEL_3);
  HAL_TIM_PWM_Start(&htim2, TIM_CHANNEL_4);

  HAL_TIM_Encoder_Start_IT(&htim4, TIM_CHANNEL_ALL);
  HAL_TIM_Encoder_Start_IT(&htim3, TIM_CHANNEL_ALL);

  // Initialize maze and set initial goal cells (center of 16x16 maze)
  Maze_Init(&maze);
  Set_Goal_Cell(&maze, 4);

  // Initialize mouse state to 0
  bzero(&mouse_state, sizeof(mouse_state_t));

  Clear_Profile(&forward_profile);
  Clear_Profile(&rotational_profile);
  /* USER CODE END 2 */

  /* Infinite loop */
  /* USER CODE BEGIN WHILE */
  while (1)
  {
    /* USER CODE END WHILE */

    /* USER CODE BEGIN 3 */
	  if (armed) {
		  motor_controller_enabled = true;
		  adjust_steering = true;
		  switch (mouse_mode) {
			  case TEST: // Mode for testing code without having to comment lines out
				  break;
			  case SEARCHING:
				  Search_Mode(&maze);
				  break;
			  case RACING:
				  Race_Mode(maze);
				  break;
		  }
	  }
	  else {
		  motor_controller_enabled = false;
		  adjust_steering = false;
	  }
  }
  /* USER CODE END 3 */
}

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
/* USER CODE BEGIN 4 */
void HAL_GPIO_EXTI_Callback(uint16_t GPIO_Pin) {
	if (GPIO_Pin == ARM_SW1_Pin) {       // Set to arm mode
		ARM_Button();
	}
	else if (GPIO_Pin == RACE_SW2_Pin) { // Set to race mode
		RACE_Button();
	}
	else if (GPIO_Pin == LOADMAZE_SW3_Pin) { // Load maze from memory into maze struct
		LOADMAZE_Button();
	}
}

void HAL_UART_RxCpltCallback(UART_HandleTypeDef *huart) {
	UART_Receive_Callback(huart);
}
/* USER CODE END 4 */
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


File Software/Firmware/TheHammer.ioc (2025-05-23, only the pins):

Mcu.UserName=STM32F103C8Tx
PA1.GPIO_Label=V_METER
PA1.Signal=ADCx_IN1
PA10.Signal=USART1_RX
PA11.GPIO_Label=LED_Red
PA11.Signal=GPIO_Output
PA12.GPIO_Label=LED_Blue
PA12.Signal=GPIO_Output
PA13.Signal=SYS_JTMS-SWDIO
PA14.Signal=SYS_JTCK-SWCLK
PA15.GPIO_Label=LED_Green
PA15.Signal=GPIO_Output
PA2.GPIO_Label=ML_PWM
PA2.Signal=S_TIM2_CH3
PA3.GPIO_Label=MR_PWM
PA3.Signal=S_TIM2_CH4
PA4.GPIO_Label=RECIV_FL
PA4.Signal=ADCx_IN4
PA5.GPIO_Label=RECIV_L
PA5.Signal=ADCx_IN5
PA6.GPIO_Label=ML_ENC_A
PA6.Signal=S_TIM3_CH1
PA7.GPIO_Label=ML_ENC_B
PA7.Signal=S_TIM3_CH2
PA8.GPIO_Label=ML_BWD
PA8.Signal=GPIO_Output
PA9.Signal=USART1_TX
PB0.GPIO_Label=RECIV_R
PB0.Signal=ADCx_IN8
PB1.GPIO_Label=RECIV_FR
PB1.Signal=ADCx_IN9
PB10.GPIO_Label=EMIT_L
PB10.Signal=GPIO_Output
PB11.GPIO_Label=EMIT_R
PB11.Signal=GPIO_Output
PB12.GPIO_Label=EMIT_FR
PB12.Signal=GPIO_Output
PB13.GPIO_Label=MR_FWD
PB13.Signal=GPIO_Output
PB14.GPIO_Label=ML_FWD
PB14.Signal=GPIO_Output
PB15.GPIO_Label=MR_BWD
PB15.Signal=GPIO_Output
PB4.GPIO_Label=ARM_SW1
PB4.Signal=GPXTI4
PB5.GPIO_Label=EMIT_FL
PB5.Signal=GPIO_Output
PB6.GPIO_Label=MR_ENC_B
PB6.Signal=S_TIM4_CH1
PB7.GPIO_Label=MR_ENC_A
PB7.Signal=S_TIM4_CH2
PB8.GPIO_Label=BUZZER
PB8.Signal=GPIO_Output
PB9.GPIO_Label=LOADMAZE_SW3
PB9.Signal=GPIO_Input
PC13-TAMPER-RTC.GPIO_Label=LED_Power
PC13-TAMPER-RTC.Signal=GPIO_Output
PC14-OSC32_IN.GPIO_Label=RACE_SW2
PC14-OSC32_IN.Signal=GPXTI14

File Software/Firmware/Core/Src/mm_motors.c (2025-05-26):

/* mm_motors.c
 *
 * File for the implementation of motor control
 */

#include "mm_motors.h"
#include "mm_supplemental.h"
#include "mm_systick.h"
#include "mm_profiles.h"

//#define FEEDFORWARD_ENABLE

extern float delta_position_forward;
extern float delta_position_rotational;

extern profile_t rotational_profile;
extern bool motor_controller_enabled;

extern const float MOUSE_RADIUS;
extern mouse_state_t mouse_state;

const float RADIANS_PER_DEGREE = 2 * M_PI / 360.0;

const float MAX_MOTOR_VOLTAGE = 6.0;
const uint16_t MAX_PWM = 2047;
const uint16_t PWM_LIMIT = 0.72 * MAX_PWM;

const float SYSTICK_FREQUENCY = 500.0;
const float SYSTICK_INTERVAL = (1.0 / SYSTICK_FREQUENCY);

const float FWD_KM = 257.0; // slope mm/s/volt
const float FWD_TM = 0.1; // time constant

const float ROT_KM = FWD_KM * 1.3; // slope dg/s/volt 1.3
const float ROT_TM = 0.1; // time constant

const float FWD_ZETA = 0.707; // sqrt(1/2) smaller is more agressive, larger is slower
const float FWD_TD = FWD_TM;  // fwd_tm
const float FWD_KP = 16 * FWD_TM / (FWD_KM * FWD_ZETA * FWD_ZETA * FWD_TD * FWD_TD);
const float FWD_KD = SYSTICK_FREQUENCY * (8 * FWD_TM - FWD_TD) / (FWD_KM * FWD_TD);

const float ROT_ZETA = 0.707;
const float ROT_TD = ROT_TM;
const float ROT_KP = 16 * ROT_TM / (ROT_KM * ROT_ZETA * ROT_ZETA * ROT_TD * ROT_TD); // 16
const float ROT_KD = SYSTICK_FREQUENCY * (8 * ROT_TM - ROT_TD) / (ROT_KM * ROT_TD); // 8

float forward_error = 0;
float previous_forward_error = 0;
float rotational_error = 0;
float previous_rotational_error = 0;

float motor_left_previous_speed = 0;
float motor_right_previous_speed = 0;

bool motor_controller_enabled = false;

void Set_Motor_Volts(motor_t motor, float voltage_to_translate) {
	voltage_to_translate = voltage_to_translate > MAX_MOTOR_VOLTAGE ? MAX_MOTOR_VOLTAGE : voltage_to_translate;
	voltage_to_translate = voltage_to_translate < -MAX_MOTOR_VOLTAGE ? -MAX_MOTOR_VOLTAGE : voltage_to_translate;

	int counter_period = MAX_PWM * (voltage_to_translate + Calculate_Battery_Bias(voltage_to_translate)) / mouse_state.battery_voltage;
	if (counter_period < 0) {
		Set_Direction(motor, REVERSE);
		counter_period = -counter_period;
	}
	else if (counter_period > 0) {
		Set_Direction(motor, FORWARD);
	}

	Set_PWM(motor, counter_period);
}

void Set_PWM(motor_t motor, uint16_t counter_period) {
	// Software limit for motor voltage ~6V
	counter_period = counter_period > PWM_LIMIT ? PWM_LIMIT: counter_period;
	switch(motor) {
		case MOTOR_LEFT:
			TIM2->CCR4 = counter_period;
			break;
		case MOTOR_RIGHT:
			TIM2->CCR3 = counter_period;
			break;
	}
}

void Set_Direction(motor_t motor, motor_direction_t direction) {
	switch(motor) {
		case MOTOR_LEFT:
			switch(direction) {
				case FORWARD:
					HAL_GPIO_WritePin(ML_FWD_GPIO_Port,  ML_FWD_Pin, 1);
					HAL_GPIO_WritePin(ML_BWD_GPIO_Port, ML_BWD_Pin, 0);
					break;
				case REVERSE:
					HAL_GPIO_WritePin(ML_FWD_GPIO_Port,  ML_FWD_Pin, 0);
					HAL_GPIO_WritePin(ML_BWD_GPIO_Port, ML_BWD_Pin, 1);
					break;
				case BRAKE:
					HAL_GPIO_WritePin(ML_FWD_GPIO_Port,  ML_FWD_Pin, 0);
					HAL_GPIO_WritePin(ML_BWD_GPIO_Port, ML_BWD_Pin, 0);
					break;
			}
			break;
		case MOTOR_RIGHT:
			switch(direction) {
				case FORWARD:
					HAL_GPIO_WritePin(MR_FWD_GPIO_Port,  MR_FWD_Pin, 1);
					HAL_GPIO_WritePin(MR_BWD_GPIO_Port, MR_BWD_Pin, 0);
					break;
				case REVERSE:
					HAL_GPIO_WritePin(MR_FWD_GPIO_Port,  MR_FWD_Pin, 0);
					HAL_GPIO_WritePin(MR_BWD_GPIO_Port, MR_BWD_Pin, 1);
					break;
				case BRAKE:
					HAL_GPIO_WritePin(MR_FWD_GPIO_Port,  MR_FWD_Pin, 0);
					HAL_GPIO_WritePin(MR_BWD_GPIO_Port, MR_BWD_Pin, 0);
					break;
			}
			break;
	}
}

void Complete_Stop() {
	Set_Direction(MOTOR_LEFT, BRAKE);
	Set_Direction(MOTOR_RIGHT, BRAKE);

	Set_PWM(MOTOR_LEFT, 0);
	Set_PWM(MOTOR_RIGHT, 0);

	motor_controller_enabled = false;
}

float Position_Controller(float velocity) {
	float increment = velocity * SYSTICK_INTERVAL;
	forward_error += increment - delta_position_forward;
	float forward_error_difference = forward_error - previous_forward_error;
	previous_forward_error = forward_error;

	return FWD_KP * forward_error + FWD_KD * forward_error_difference;
}

float Rotational_Controller(float steering_adjustment, float omega) {
	float increment = omega * SYSTICK_INTERVAL;
	rotational_error += increment - delta_position_rotational;
	rotational_error += steering_adjustment;
	float rotational_error_difference = rotational_error - previous_rotational_error;
	previous_rotational_error = rotational_error;

	return ROT_KP * rotational_error + ROT_KD * rotational_error_difference;
}

void Update_Motors(float velocity, float omega, float steering_adjustment) {
	steering_adjustment = rotational_profile.state == IDLE || rotational_profile.state == COMPLETE ? steering_adjustment : 0;

	float position_output = Position_Controller(velocity);
	float rotational_output = Rotational_Controller(steering_adjustment, omega);

	float motor_left_voltage = 0;
	float motor_right_voltage = 0;
	motor_left_voltage = position_output - rotational_output;
	motor_right_voltage = position_output + rotational_output;

	if (motor_controller_enabled) {
		Set_Motor_Volts(MOTOR_LEFT, motor_left_voltage);
		Set_Motor_Volts(MOTOR_RIGHT, motor_right_voltage);
	}
}

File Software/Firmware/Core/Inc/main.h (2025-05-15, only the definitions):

#define LED_Power_Pin GPIO_PIN_13
#define LED_Power_GPIO_Port GPIOC
#define RACE_SW2_Pin GPIO_PIN_14
#define RACE_SW2_GPIO_Port GPIOC
#define RACE_SW2_EXTI_IRQn EXTI15_10_IRQn
#define V_METER_Pin GPIO_PIN_1
#define V_METER_GPIO_Port GPIOA
#define ML_PWM_Pin GPIO_PIN_2
#define ML_PWM_GPIO_Port GPIOA
#define MR_PWM_Pin GPIO_PIN_3
#define MR_PWM_GPIO_Port GPIOA
#define RECIV_FL_Pin GPIO_PIN_4
#define RECIV_FL_GPIO_Port GPIOA
#define RECIV_L_Pin GPIO_PIN_5
#define RECIV_L_GPIO_Port GPIOA
#define ML_ENC_A_Pin GPIO_PIN_6
#define ML_ENC_A_GPIO_Port GPIOA
#define ML_ENC_B_Pin GPIO_PIN_7
#define ML_ENC_B_GPIO_Port GPIOA
#define RECIV_R_Pin GPIO_PIN_0
#define RECIV_R_GPIO_Port GPIOB
#define RECIV_FR_Pin GPIO_PIN_1
#define RECIV_FR_GPIO_Port GPIOB
#define EMIT_L_Pin GPIO_PIN_10
#define EMIT_L_GPIO_Port GPIOB
#define EMIT_R_Pin GPIO_PIN_11
#define EMIT_R_GPIO_Port GPIOB
#define EMIT_FR_Pin GPIO_PIN_12
#define EMIT_FR_GPIO_Port GPIOB
#define MR_FWD_Pin GPIO_PIN_13
#define MR_FWD_GPIO_Port GPIOB
#define ML_FWD_Pin GPIO_PIN_14
#define ML_FWD_GPIO_Port GPIOB
#define MR_BWD_Pin GPIO_PIN_15
#define MR_BWD_GPIO_Port GPIOB
#define ML_BWD_Pin GPIO_PIN_8
#define ML_BWD_GPIO_Port GPIOA
#define LED_Red_Pin GPIO_PIN_11
#define LED_Red_GPIO_Port GPIOA
#define LED_Blue_Pin GPIO_PIN_12
#define LED_Blue_GPIO_Port GPIOA
#define LED_Green_Pin GPIO_PIN_15
#define LED_Green_GPIO_Port GPIOA
#define ARM_SW1_Pin GPIO_PIN_4
#define ARM_SW1_GPIO_Port GPIOB
#define ARM_SW1_EXTI_IRQn EXTI4_IRQn
#define EMIT_FL_Pin GPIO_PIN_5
#define EMIT_FL_GPIO_Port GPIOB
#define MR_ENC_B_Pin GPIO_PIN_6
#define MR_ENC_B_GPIO_Port GPIOB
#define MR_ENC_A_Pin GPIO_PIN_7
#define MR_ENC_A_GPIO_Port GPIOB
#define BUZZER_Pin GPIO_PIN_8
#define BUZZER_GPIO_Port GPIOB
#define LOADMAZE_SW3_Pin GPIO_PIN_9
#define LOADMAZE_SW3_GPIO_Port GPIOB

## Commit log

2024-06-30 Added base file to directory, imported custom symbols
    [bloo.kicad_pcb, bloo.kicad_sch, bloo.sch]
2024-06-30 Updated BOM with changes associated with motor driver and removal of 100k resistors
    [bloo.csv, bloo.kicad_sch]
2024-06-30 Added button, updated BOM
    [bloo.kicad_sch]
2024-07-13 Current state
    [bloo.kicad_sch]
2024-07-14 Added power ORing schematic. Updated BOM and added footprints/symbols
    [bloo.kicad_sch]
2024-07-24 Created second kicad directory for version of micromouse without bluepill (using solely STM chip). Updated BOM accordingly and updated schematic for said file
    [bloo.csv, bloo.kicad_pcb, bloo.kicad_sch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]
2024-07-26 Reviewed and updated schematics accordingly, updated BOM, created PCB Design Notes
    [bloo.kicad_pcb, bloo.kicad_sch]
2024-08-01 Completed routing for version using bluepill, no DRC errors. Began routing for version with no bluepill
    [bloo.kicad_pcb, bloo.kicad_sch]
2024-08-04 Completed routing of non-bluepill version of schematic. All DRC errors cleared. Version/Name/Year label updated. To be reviewed.
    [bloo.kicad_pcb]
2024-08-07 Adjusted dielectric stackup thickness to 1.6mm. Both PCBs have been reviewed, TB manufactured.
    [bloo.kicad_pcb]
2024-08-08 Updated silkscreen, generated gerber and drill files. Placed PCB orders.
    [bloo-B_Cu.gbl, bloo-B_Mask.gbs, bloo-B_Paste.gbp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]
2024-08-17 Added shortcut to soldering checklist. All parts received, begin testing of new mouse
2024-08-23 Added schematic PDF
2024-11-15 Updated bluepill version of mouse to use L293D motor driver rather than TB6612FNG
    [bloo.kicad_pcb, bloo.kicad_sch]
2024-11-15 Added API.cpp, API.h from mackarone micromouse simulator. Created main file and created layout based on my previous software
    [bloo.csv, bloo.kicad_pcb]
2024-11-24 Completed Floodfill function
    [bloo.kicad_pcb, bloo.kicad_sch]
2024-11-24 Discovered bug with scanWalls and scanWallsAdjacent - Need to debug
    [Main.cpp]
2024-12-13 Resolved sim update errors, completed maze solving sim algorithm
    [bloo.kicad_pcb]
2025-02-22 Added interrupt for UART communication across bluetooth link. Configured clock settings in IOC to use internal clock.
    [bloo.kicad_sch]
2025-02-23 Added mm_commands files for implementation of UART command parsing and data transmit
2025-02-27 Added directory and file outline for Bluetooth communication and GUI. Started creating GUI using tkinter, not currently functional.
2025-02-28 Added essential functionality to GUI. Added expadnable command parsing. Added fit to window frames.
2025-02-28 Added data field to data frame. Created file for maze translation. Implemented regular calls to listen for data and update accordingly.
2025-03-02 Implemented pair, disconnect, send, receive using pyserial. Began implementation of debug mode and PAIRED command. Currently unstable
    [CoolNameForMouseHere.ioc, Main.cpp, main.c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]
2025-03-04 Implemented rest of current commands on client side. Implemented maze file creation. New commands untested.
2025-03-07 If paired receives no response, updates GUI and disconnects socket
2025-03-07 Fixed packet alignment for 24 byte packets.
    [bloo.kicad_pcb]
2025-03-08 Completed maze translation scheme. File write back can still be improved to be correctly visualized in file, but works when loaded into GUI.
    [mm_bluetooth_gui.py, mm_bluetooth_parse.py, mm_commands.c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]
2025-03-25 Fixed formatting of IR byte data.
    [main.c, mm_bluetooth_parse.py, mm_params.py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]
2025-04-02 Added mouse state struct to hold debug information. Implemented low level motor control software, modified IOC accordingly.
2025-04-04 Experimental encoder code. Not working currently.
    [TheHammer.ioc, main.c, main.h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]
2025-04-05 Encoders working. RPM calculation tested.
2025-04-14 Integrated floodfill module into firmware package. Implemented button functionality. Fixed encoder ticking in wrong direction.
    [TheHammer.ioc, main.c, main.h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]
2025-05-13 Wrote bulk of profile code. Calibrated battery readings and PWM outputs.
2025-05-15 Tuned constants. Added blocks for steering adjustments.
2025-05-18 Bug fixes. Implemented search mode. Currently doesn't build.
    [main.c, mm_encoders.c, mm_floodfill.c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]
2025-05-20 Implemented non-smooth turns. Unstable, could be because low battery voltage and variable lighting. Rotational and positional controller need tuning. Floodfill unstable, could have incorrect walls be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
    [mm_floodfill.c, mm_motors.c, mm_profiles.c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]
2025-05-21 Normal turns. Non smooth motion. Fixed 180 for return to start position. Unstable.
    [mm_floodfill.c, mm_motors.c, mm_supplemental.c]
2025-05-23 Tuned values. Modified how parameters are packed and passed for profiles. Began work on race mode in simulator <- unstable.
    [Main.cpp, TheHammer.ioc, main.c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]
2025-05-25 Real final commit. Tuned values. Fixed enter goal, fixed start after full run completion.
    [main.c, mm_floodfill.c, mm_vision.c]
2025-05-26 Removed remnants of feedforward. Fixed spelling errors.
    [main.c, mm_floodfill.c, mm_motors.c]

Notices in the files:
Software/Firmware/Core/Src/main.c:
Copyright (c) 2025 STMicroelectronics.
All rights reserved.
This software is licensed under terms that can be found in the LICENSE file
